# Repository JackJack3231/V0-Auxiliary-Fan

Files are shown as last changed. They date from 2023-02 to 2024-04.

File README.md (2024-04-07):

# V0 Auxiliary Cooling Fan

Auxiliary Cooling Fan Ducts for the Voron V0 3d-Printers, using either a 5015, 6028, 7530, 9733 or 12032 Blower fans.
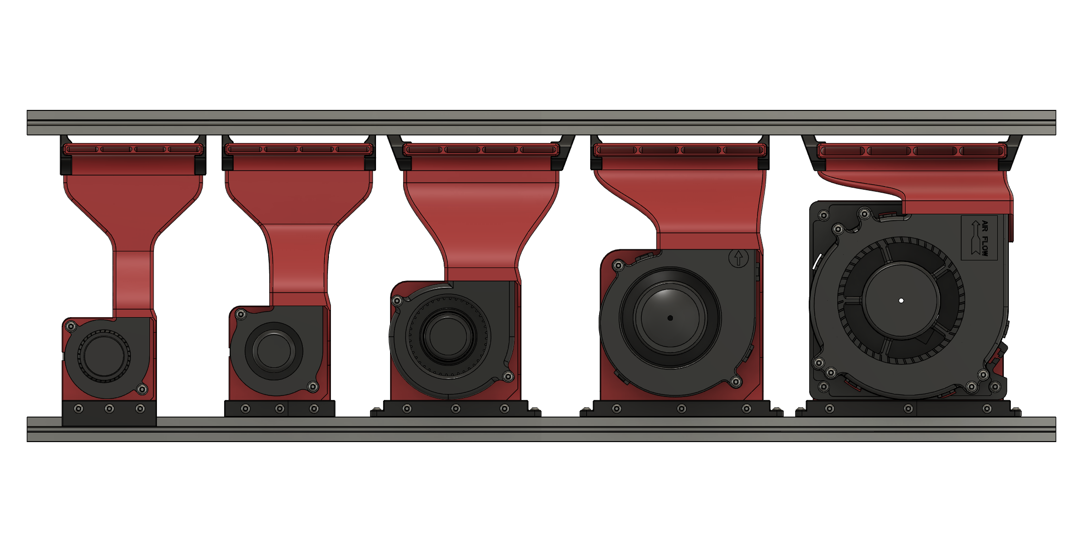
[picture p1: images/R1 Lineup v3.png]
Lineup of all Ducts


Below the 6028 Fan and duct installed in a v0.2 using the screw mounts.
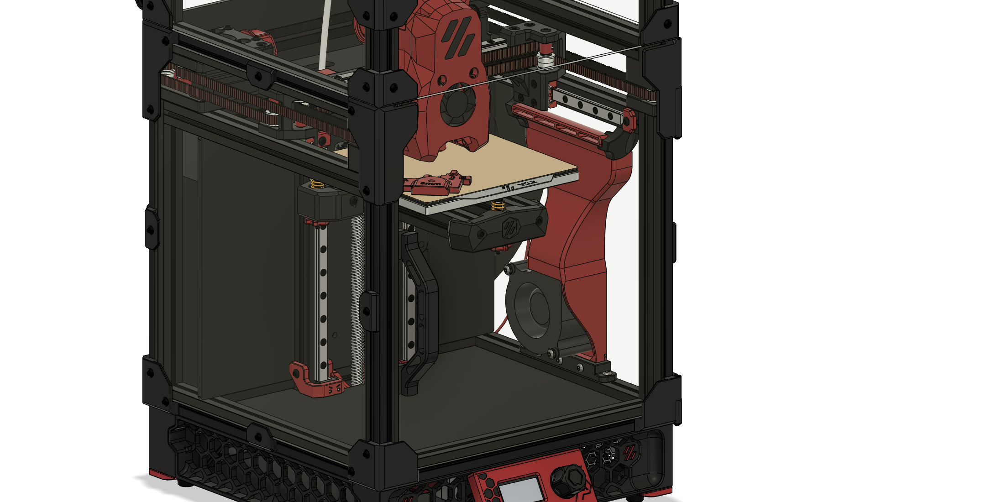
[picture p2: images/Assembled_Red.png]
5015 Fan installed


The ducts can be easily installed after the Printer has already been fully assembled, as there are mounting options that don't require preloaded nuts in the extrusion slots.

Since the [R1 release](#2023-08-15-R1-Release) there are now 3 mounting options:

1. (Legacy) Clamp-Mount: this one just clamps the duct to the bottom extrusion. This was an easy way to secure the ducts, however the ducts were prone to come loose from vibrations and could tilt into the print volume, colliding with the toolhead. This version is no longer recommended.
2. Screw-Mounts to secure the bottom and top of the ducts to the frame. These allow the most secure installation, however you will need preloaded M3 nuts in the slots of the extrusion (2 at the bottom and 2 at the top). Due to space constraints installing these Mounts (especially the top ones) can be rather difficult on the larger fan ducts with the frame assembled.
3. Twist-Mounts that get inserted into the extrusion slot and twisted 90° to secure to the frame. These provide a very solid mount while not needing preloaded M3 nuts and therefore are the recommended installation method for already fully assembled printers. If these are too tight or too loose after installation you can adjust the CAD-Files to improve the mount, a [guide is provided in the docs folder](docs/CAD_Twist_Tightness.md). There also is an alternative stronger version of the bottom twist mounts which don't rely on layer adhesion as much and should therefore be much stronger than the standard ones. The stronger mounts require 2 additional Heatsets and M3x12 screws.

All of these mounting options use the same main duct bodies, so you could also mix and match as you want. For Example if you used a Nevermore filter before you could use the 2 M3 nuts in the bottom extrusion to secure the bottom of the duct with a screw mount and the top with the twist mounts.

**No matter what mount you choose it is highly recommended you use one of the top mounts to ensure proper alignment towards the print bed and avoid the duct to collide with the toolhead.**

The ducts come in 2 Versions: A Unibody Version for which you'll need a larger Printer as it is 170 mm long and a 2 Piece Version which you can print on a V0 and glue together after printing.

I have not done any CFD-Simulation on these shrouds, so they definitely could be better.

Currently, there are ducts for the following Blower Fan sizes available:

- [50x15mm](/ducts/5015/)
- [60x28mm](/ducts/6028/)
- [75x30mm](/ducts/7530/)
- [97x33mm](/ducts/9733/)
- [120x32mm](/ducts/12032/)

There also are ducts that target their airflow 3 mm lower than the MiniSB for people using higher flow toolheads where the nozzle sits slightly lower in the [UHF Folder](ducts/_UHF/). **This is not required for High-Flow setups that don't change the nozzle height like chirpy's [Rapid Burner](https://github.com/chirpy2605/voron/tree/main/V0/Rapid_Burner)**.

I also started adding ducts, that I was requested to make for specific setups, to the repo. You will find these in the [Customs Folder](/ducts/_Customs/).

### Warning about Tolerances

There seems to be quite a bit of variance in the exact mounting hole patterns on these blower fans, especially the larger ones. So you could run into compatibility issues and need to adjust the model in CAD. I used GDSTIME fans for all my tests, so these should work.

Additionally, the width of the slots on the MakerBeamXL or LDO Extrusions can vary a lot. These generally are specced at 3-3.2 mm wide. The ducts were designed with a 3.2 mm thick part that slots into the extrusion. This was made to ensure a snug fit, however on some frames it could be very difficult/impossible to slot in. So either you can just print it and sand down the bottom part if needed or measure your frame before printing and adjust in CAD for the measured slot thickness.

### Overhang Test

For Comparison Pictures of the cooling Performance check the [Overhang Tests](/docs/OverhangTests.md) Document. These are currently outdated as they use the old ducts from before the R1 Release.

## Print Settings

As these parts don't hold any high loads you don't have to print these according to the Voron Guidelines. 3 Perimeters with 25% Infill are more than enough.

## Stuff to keep in mind

### Connecting the fan

You'll need a way to connect the fan, there are a few ways to do this outlined in the [Connecting the fan](/docs/connecting_fan.md) documentation.

### Shroud Clearance

If you have LEDs or a Camera mounted to the underside of the Y-axis extrusions these will likely collide with the fanshroud, so you might need to move the LEDs to the top.

## BOM

Depending on your choice of mount and fan the BOM changes. The parts for the mounts are the same, regardless of fan:
| Part | Quantity | Notes |
| --- | --- | --- |
| M3x5x4 Heatset Insert | 3 | for all mounts |
| M3x16 BHCS | 3 | for clamp mount |
| M3x12 BHCS | 2 | for screw and twist mount |
| M3x8 BHCS | 2 | for bottom screw mount |
| M3x6 BHCS | 2 | for top screw mount |
| Superglue | | only if using a 2 piece duct |
| VHB-Tape | | for top mounts |

**For the stronger twist mounts you will need 2 more Heatsets and M3x12 screws, so 5 Heatsets and 5 M3x12 screws in total.**

BHCS can be substituted for SHCS.

Additionally, you will need some Hardware to secure the fan. See the specific README of each version for a list of additionally required parts.

## Assembly instructions

Refer to the [General Assembly Instructions](/docs/general_assembly.md) documentation and the additional information in the README of each specific duct.

## Firmware Configuration

There are example klipper configs with macros and display entries provided. These allow easy control of the fan and even Slicers like BambuStudio or OrcaSlicer to control the fan with G-Code.

Refer to the [Firmware and Slicer Configuration](/docs/firmware_slicer.md) documentation.

## Credits

Thanks to the Voron Team for their great work on the V0 Printer: [Voron Design](https://vorondesign.com/voron0.2)

Following Fan Models were used in CAD:

- [Radial Cooling 5015 Fan (50 mm) DC12V](https://grabcad.com/library/radial-cooling-5015-fan-50mm-dc12v-1) by
  Aleksandr Ivanov
- [Basic 6028 Blower Model](https://www.thingiverse.com/thing:4270101) by kelvinA
- [Gamma 28 Blower Fan 76×30 mm](https://grabcad.com/library/gamma-28-blower-fan-76x30mm-1) by Pokai Chang
- [CBM-979433S-125-467](https://www.cuidevices.com/product/thermal-management/dc-fans/centrifugal-blowers/cbm-979433s-125-467) by CUI Devices
- [CBM-A232B-120-457](https://www.cuidevices.com/product/thermal-management/dc-fans/centrifugal-blowers/cbm-a232b-120-457) by CUI Devices

## Changelog

### 2024-04-07
- Add WIP Dual 5015 duct

### 2024-02-14
- Add 12032 Hex-Zero variant
- Add Stronger Bottom Twist Mount Variant. This does not rely on layer adhesion nearly as much as the standard version, so it should be a lot stronger. However, you will need 2 additional Heatsets and 2 M3x12 screws.
- Moved Mounts to separate sub-folders for better organization

### 2023-12-23

- Updated slot-bar to be a bit flexible and increase compatibility with different extrusion slot widths, while still providing some stiffness
- Added first custom duct model for the Hex-Zero with a 75x30 mm blower

### 2023-08-25

- Add experimental 5015 & 6028 ducts with clearance for klicky probes

### 2023-08-15 R1 Release

- Remade all ducts to make CAD cleaner, wall thicknesses more consistent and the design more consistent overall
- Adjusted ducts to reduce back pressure and improve overall cooling performance (12032 Version seems to still have a bit of a back pressure issue, but is far better than the old design).
- Increased thickness of bottom bar that slots into the extrusion for more rigid mount. Tolerances of these slots are quite big, so on some frames it could get tight.
- Added Cable-Channels to rear for tidier wire routing
- Added Screw-Mounts for the bottom and the top of the ducts (Require preloaded M3 nuts)
- Added "Twist"-Mounts for the bottom and the top of the ducts
- Improvements to Supports, resulting in better print results. However, these are slightly harder to remove.
- In addition to STEP Files I also exported the source Fusion 360 Files, allowing for easier Modification and understanding of how these ducts were created.
- Updated Documentation to reflect these changes
- Added links to the used CAD-Files for the fans

Changes made to ducts to improve cooling performance:

- 6028: Duct Outlet is now 85 mm wide (before 80 mm)
- 7530: Duct Outlet is 90 mm wide and 3.5 mm high (before 80 mm and 3 mm respectively)
- 9733: Duct Outlet is 100 mm wide and 4 mm high (before 80 mm and 3 mm respectively)
- 12032: Duct Outlet is 110 mm wide and 5 mm high (before 90 mm and 3 mm respectively)

All had slight changes to the internal flow guide geometry to (hopefully) improve cooling performance.

Known Issue: The 7530 duct still has higher airflow on the left side than on the right side, at least at 100% speed. Will need to rework the internal flow guides some time in the future.

### 2023-06-24

- Add centered Top Part for the 12032 Duct for better alignment when installed on the left side of the printer. Deprecated old version.

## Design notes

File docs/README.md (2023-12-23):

# Documentation

In this folder you will find some general documentation, that has been split into extra files to keep the README files to a reasonable Length.

## Current Documentation

### CAD Guide: [Adjusting Duct Height](CAD_Outlet_Height.md)

### CAD Guide: [Adjusting Twist Mount Tightness](CAD_Twist_Tightness.md)

### [Options to connect the fan](connecting_fan.md)

### [Firmware and Slicer configuration](firmware_slicer.md)

### [General Assembly Instructions](general_assembly.md)

### [Overhang Tests](OverhangTests.md)

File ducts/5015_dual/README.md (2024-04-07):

# WIP: Dual 5015 Blower Fan Duct

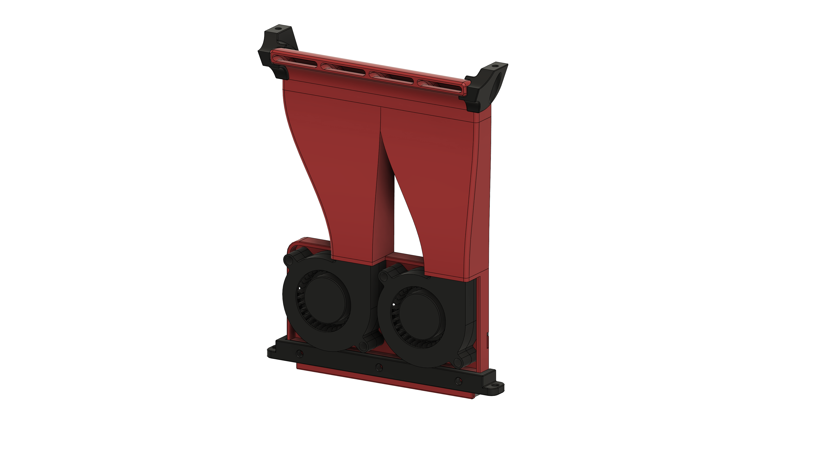
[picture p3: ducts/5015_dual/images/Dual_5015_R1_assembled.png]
Dual 5015 Duct


## WIP
**Currently this variant is untested!**

 - There is no 2 Piece variant available, so you need a large enough printer to print these parts
 - For the bottom twist mount there is only the "strong" variant available

## BOM
These parts are required in addition to the [General BOM](/README.md#bom)
| Part | Quantity | Notes |
| --- | --- | --- |
| M3x5x4 Heatset Insert | 4 | |
| 5015 Blower Fan | 2 | 5V or 24V depending on your setup |
| M3x20 BHCS | 4 | M3x18 also works, then you don't need the printed spacer |
| M3 Washer | 4 | optional, only to make better contact with the fan |

## Printed Parts

Print the parts according to your choice of mount. If you are using M3x20 BHCS don't forget to print 2 of the spacers.

## Assembly Instructions
Follow the [General Assembly Instructions](/docs/general_assembly.md).

To secure the fans to the duct use the M3x20 BHCS with a washer and the printed spacer. Alternatively use M3x18 BHCS with a washer but without the spacer.

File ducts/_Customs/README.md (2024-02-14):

# Custom fan ducts

In this folder you will find ducts that I made upon request for specific setups.
Feel free to reach out to me if you need a custom duct made for your printer and fan setup, however I cannot guarantee that I will have the time to actually make it.

Also, I will only update these upon request.

BOM is generally the same as the standard versions unless specifically called out.

| Printer/Setup | Notes | Link to Printer |
| --- | --- | --- |
| [75x30 mm for Hex-Zero](Hex-Zero/7530/) | Designed only for the right side, as left has the Probe Dock | [Hex-Zero GitHub](https://github.com/Alexander-T-Moss/Hex-Zero) |
| [120x32 mm for Hex-Zero](Hex-Zero/12032/) | Designed only for the right side, as left has the Probe Dock | [Hex-Zero GitHub](https://github.com/Alexander-T-Moss/Hex-Zero) |

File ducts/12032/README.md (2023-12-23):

# 12032 Blower Fan Duct

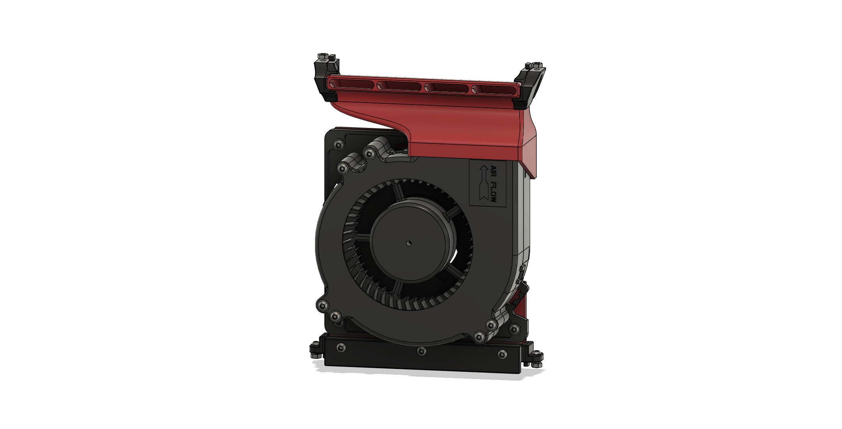
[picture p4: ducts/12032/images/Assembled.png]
12032 Duct Assembled


## BOM

| Part | Quantity | Notes |
| --- | --- | --- |
| M3x5x4 Heatset Insert | 9 | |
| 12032 Blower Fan | 1 | 5V or 24V depending on your setup |
| M3x8 BHCS | 3 | |
| M3x35 BHCS | 6 | |
| M3 Washer | 9 | optional, only to make better contact with the fan |

These numbers of screws and Heatsets are to populate all the mounting holes of the fan.

The Fan I used was this [GDSTIME 12032 24V Dual Ball Bearing Blower Fan](https://www.aliexpress.com/item/1005005288258849.html)

## Printed Parts

Print the parts according to your choice of mount.

## Assembly Instructions

Follow the [General Assembly Instructions](/docs/general_assembly.md).

To secure the fan to the duct use the M3x8 BHCS with a washer to secure the corners of the fan and the M3x35 BHCS with a washer to secure the remaining 6 inner holes.

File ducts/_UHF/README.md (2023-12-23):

# UHF Ducts
Here you will find ducts with a 3 mm lower outlet to better target the air for longer toolheads/Hotends.

**These are not required for High Flow setups that don't change the nozzle height, like chirpy's [Rapid Burner](https://github.com/chirpy2605/voron/tree/main/V0/Rapid_Burner). If your setup has the nozzle at the same height as the stock Mini-Stealthburner you will need the "standard" ducts instead.**

If you need a different height for the outlet there is a [guide to edit the base Fusion360 CAD Files](/docs/CAD_Outlet_Height.md) in the docs' folder.

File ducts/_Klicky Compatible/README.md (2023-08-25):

# Klicky compatible fan ducts
These ducts are designed to leave space at the front right corner for the klicky mounts are lower to make space for the carrier part on the cowling and blow the air across the bed at an angle.

**These are completely untested and highly experimental!**

So far there are unibody ducts for the 5015 and 6028 fans. The bottom mounts are the same as for the standard ducts. Due to the angle of the ducts there are new top mounts.

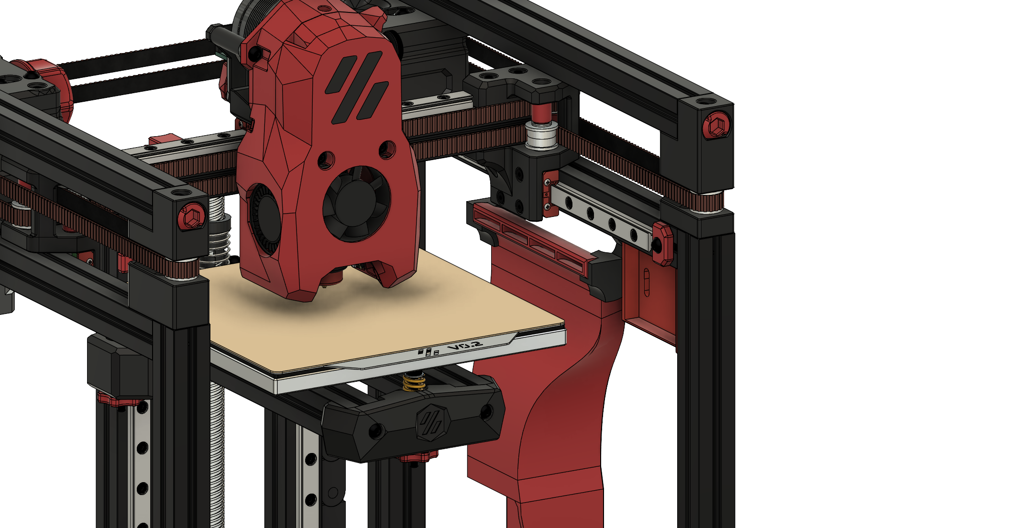
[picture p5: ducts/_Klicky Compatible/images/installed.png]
Installed Duct


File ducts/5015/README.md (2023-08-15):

# 5015 Blower Fan Duct

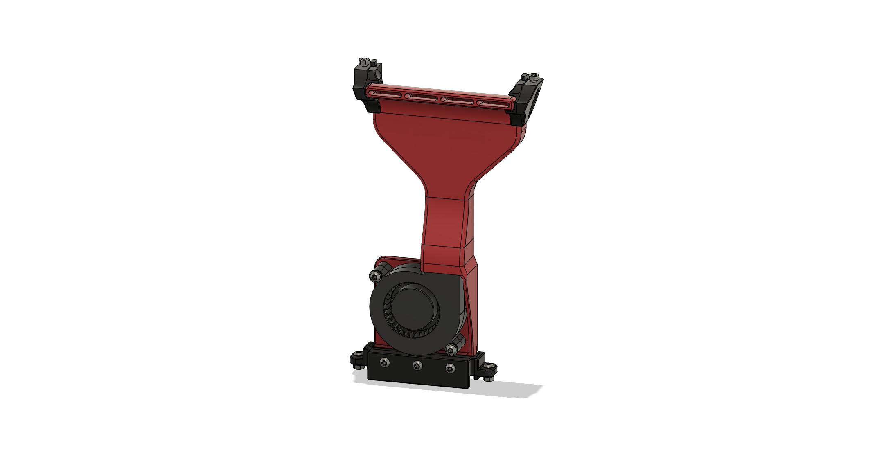
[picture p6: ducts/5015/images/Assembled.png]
5015 Duct Assembled


## BOM
These parts are required in addition to the [General BOM](/README.md#bom)
| Part | Quantity | Notes |
| --- | --- | --- |
| M3x5x4 Heatset Insert | 2 | |
| 5015 Blower Fan | 1 | 5V or 24V depending on your setup |
| M3x20 BHCS | 2 | M3x18 also works, then you don't need the printed spacer |
| M3 Washer | 2 | optional, only to make better contact with the fan |

The Fan I used was this [GDSTIME 5015 24V Dual Ball Bearing Blower Fan](https://www.aliexpress.com/item/32865977791.html)

## Printed Parts

Print the parts according to your choice of mount. If you are using M3x20 BHCS don't forget to print 2 of the spacers.

## Assembly Instructions
Follow the [General Assembly Instructions](/docs/general_assembly.md).

To secure the fan to the duct use the M3x20 BHCS with a washer and the printed spacer. Alternatively use M3x18 BHCS with a washer but without the spacer.

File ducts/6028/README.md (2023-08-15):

# 6028 Blower Fan Duct

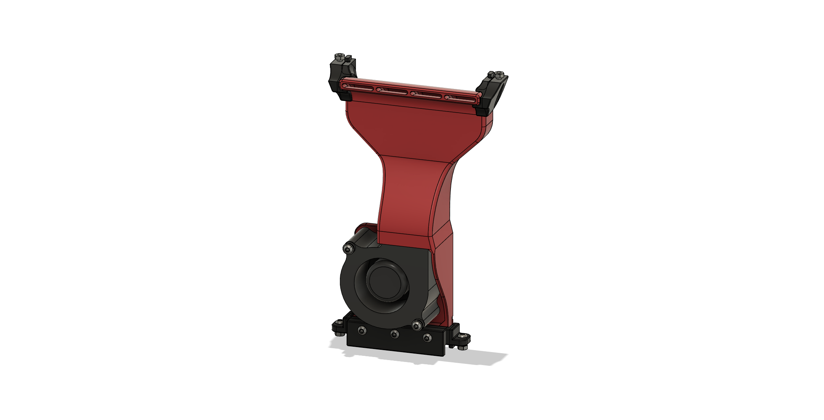
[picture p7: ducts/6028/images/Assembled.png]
6028 Duct Assembled


## BOM
These parts are required in addition to the [General BOM](/README.md#bom)
| Part | Quantity | Notes |
| --- | --- | --- |
| M3x5x4 Heatset Insert | 2 | |
| 6028 Blower Fan | 1 | 5V or 24V depending on your setup |
| M3x35 BHCS | 2 | |
| M3 Washer | 2 | optional, only to make better contact with the fan |

The Fan I used was this [GDSTIME 6028 24V Dual Ball Bearing Blower Fan](https://www.aliexpress.com/item/1005003792895461.html)

## Printed Parts

Print the parts according to your choice of mount. Print 2 of the spacers for use with the M3x35 BHCS.

## Assembly Instructions
Follow the [General Assembly Instructions](/docs/general_assembly.md).

To secure the fan to the duct use the M3x35 BHCS with a washer and the printed spacer.

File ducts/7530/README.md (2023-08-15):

# 7530 Blower Fan Duct

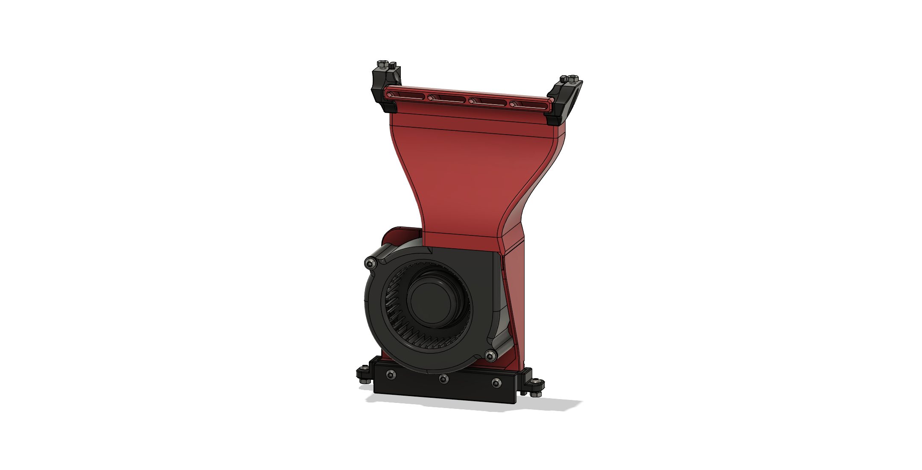
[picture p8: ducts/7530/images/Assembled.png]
7530 Duct Assembled


## BOM
These parts are required in addition to the [General BOM](/README.md#bom)
| Part | Quantity | Notes |
| --- | --- | --- |
| M3x5x4 Heatset Insert | 2 | |
| 7530 Blower Fan | 1 | 5V or 24V depending on your setup |
| M3x35 BHCS | 2 | |
| M3 Washer | 2 | optional, only to make better contact with the fan |

The Fan I used was this [GDSTIME 7530 24V Dual Ball Bearing Blower Fan](https://www.aliexpress.com/item/1005002663971820.html)

## Printed Parts

Print the parts according to your choice of mount. Print 2 of the spacers for use with the M3x35 BHCS.

## Assembly Instructions
Follow the [General Assembly Instructions](/docs/general_assembly.md).

To secure the fan to the duct use the M3x35 BHCS with a washer and the printed spacer.

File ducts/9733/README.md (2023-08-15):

# 9733 Blower Fan Duct

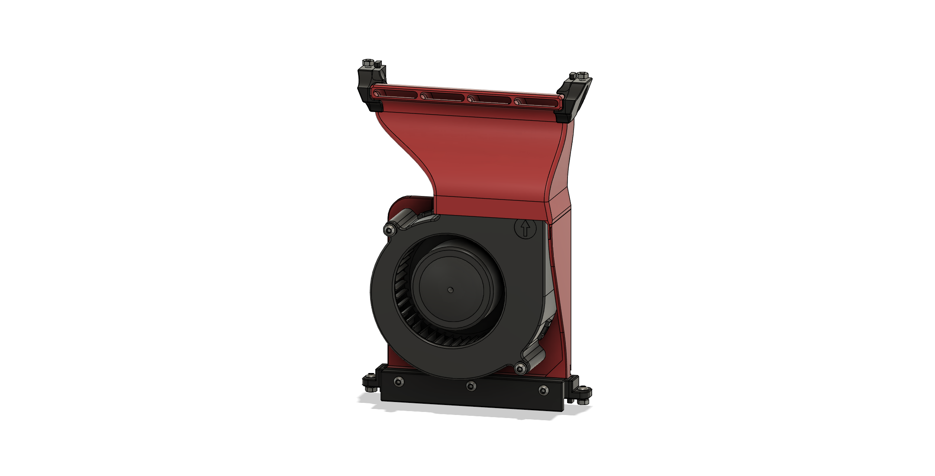
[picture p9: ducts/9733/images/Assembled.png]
9733 Duct Assembled


## BOM

These parts are required in addition to the [General BOM](/README.md#bom)
| Part | Quantity | Notes |
| --- | --- | --- |
| M3x5x4 Heatset Insert | 2 | |
| 9733 Blower Fan | 1 | 5V or 24V depending on your setup |
| M3x40 BHCS | 2 | |
| M3 Washer | 2 | optional, only to make better contact with the fan |

The Fan I used was this [GDSTIME 9733 24V Dual Ball Bearing Blower Fan](https://www.aliexpress.com/item/32622626365.html)

## Printed Parts

Print the parts according to your choice of mount. Print 2 of the spacers for use with the M3x40 BHCS.

## Assembly Instructions

Follow the [General Assembly Instructions](/docs/general_assembly.md).

To secure the fan to the duct use the M3x40 BHCS with a washer and the printed spacer.

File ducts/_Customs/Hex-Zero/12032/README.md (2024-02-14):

# 12032 for Hex-Zero

Custom designed duct and mount to fit the ginormous 12032 Blower fans into a Hex-Zero.

**This is currently untested.** Especially the clearance for the z-axis drag chain could be problematic, a "fixed" chain end on the rail mount is recommended to prevent the drag chain from rubbing against the fan body.
The wall thickness was also reduced to 1 mm from 2 mm to make space for the ducting, however this also means that the duct part is weaker.

All the printed parts were made specifically for the Hex-Zero and none of the original duct are reused.

Also, the way the bottom mount and duct attach to the fan has changed, you will need to install 3 Heatsets into the 3 outer mounting holes of the Blower Fan (see [Heatset Locations](#heatset-locations)).

## BOM

| Part | Quantity | Notes |
| --- | --- | --- |
| M3x5x4 Heatset Insert | 3 | |
| 12032 Blower Fan | 1 | 5V or 24V depending on your setup |
| M3x12 BHCS | 2 | |
| M3x6 BHCS | 1 | |

If you use the screw mounts you will need a M3x6 BHCS and M3 Nut for each mounting point (4 in total, 2 for the bottom and 2 for the top mounts).

## Printed Parts
You will need to print:
- 1x 12032_R1_Hex-Zero_Right_Top
- 2x Top Mount of your choice (Screw or Twist)
- 2x Bottom Mount of your choice (Screw or Twist)

## Images
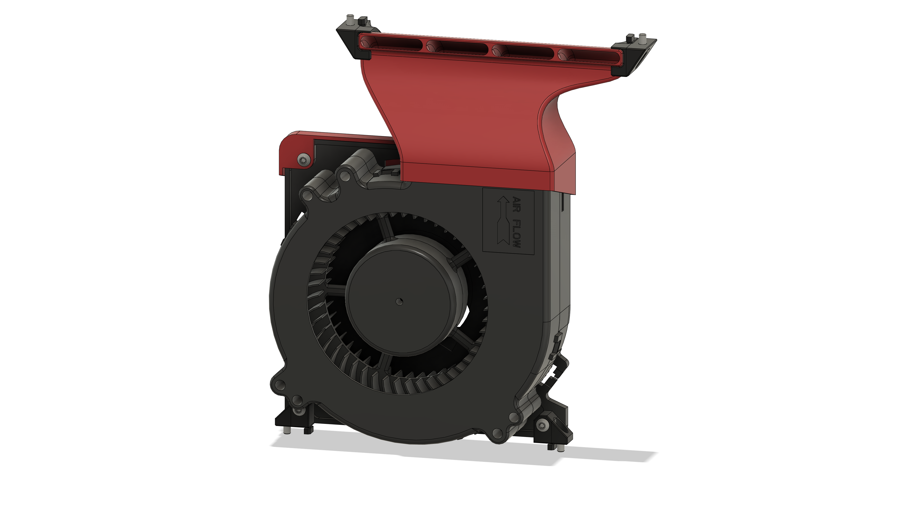
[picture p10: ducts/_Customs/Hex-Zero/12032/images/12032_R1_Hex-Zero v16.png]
12032 Hex-Zero

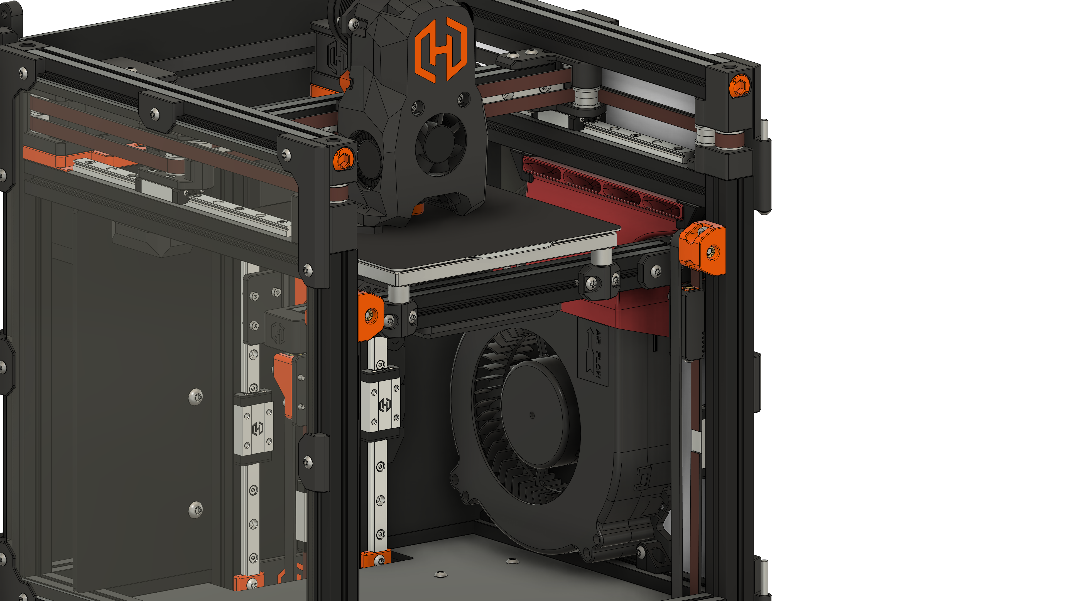
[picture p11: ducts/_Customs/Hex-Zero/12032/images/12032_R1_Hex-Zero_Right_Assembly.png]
12032 Hex-Zero Installed

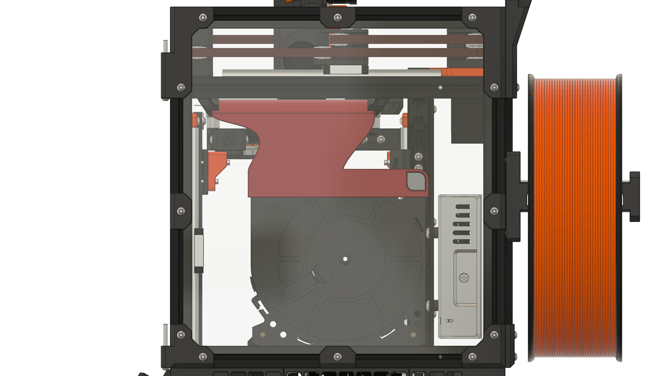
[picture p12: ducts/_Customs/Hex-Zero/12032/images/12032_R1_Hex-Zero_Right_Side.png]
12032 Hex-Zero Bed clearance


### Heatset Locations
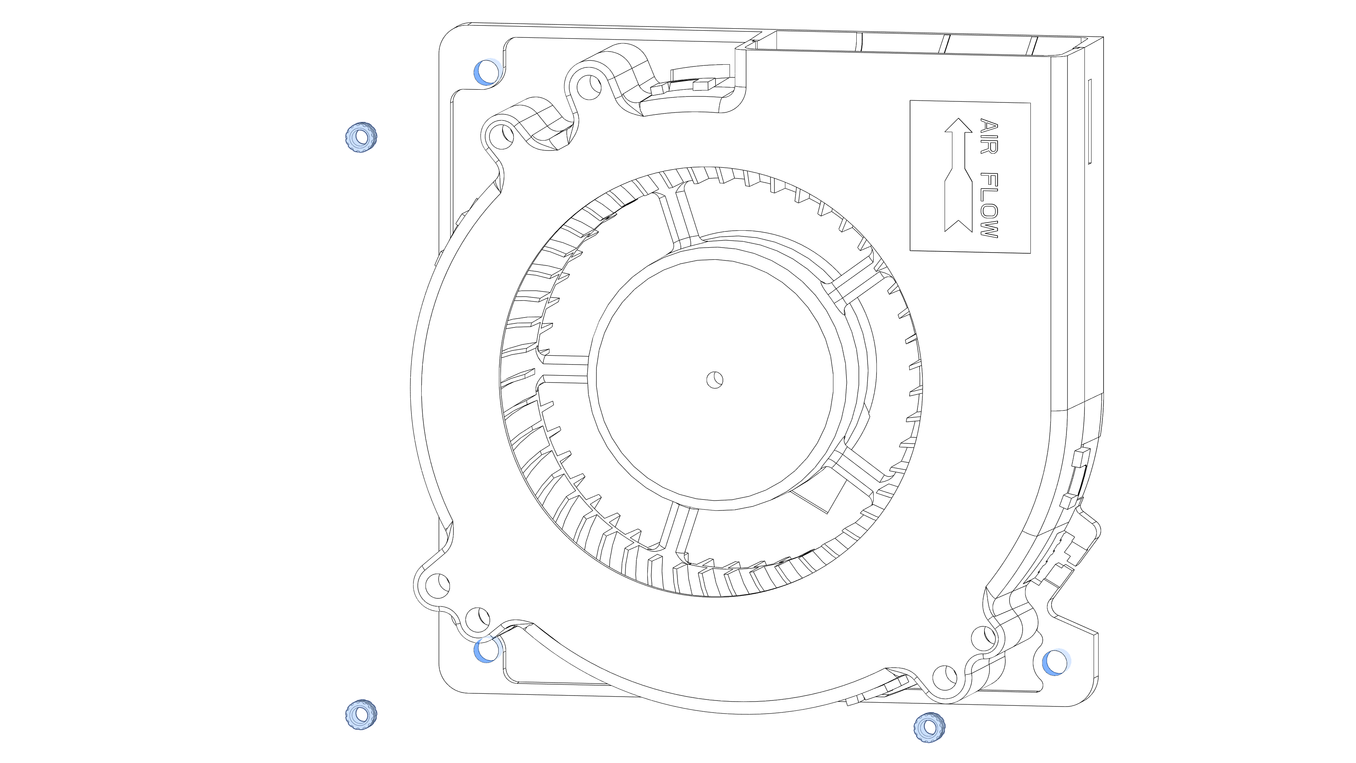
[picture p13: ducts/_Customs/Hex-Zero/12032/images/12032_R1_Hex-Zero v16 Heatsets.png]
12032 Hex-Zero Heatsets


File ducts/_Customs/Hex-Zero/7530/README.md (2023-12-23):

# 7530 for Hex-Zero

Custom designed duct to have the outlet at the proper height and clear the Bed Assembly.
The duct is confirmed to fit and work.

The bottom mount parts are the same as the standard duct, so get your choice from the [7530 folder](/ducts/7530/).

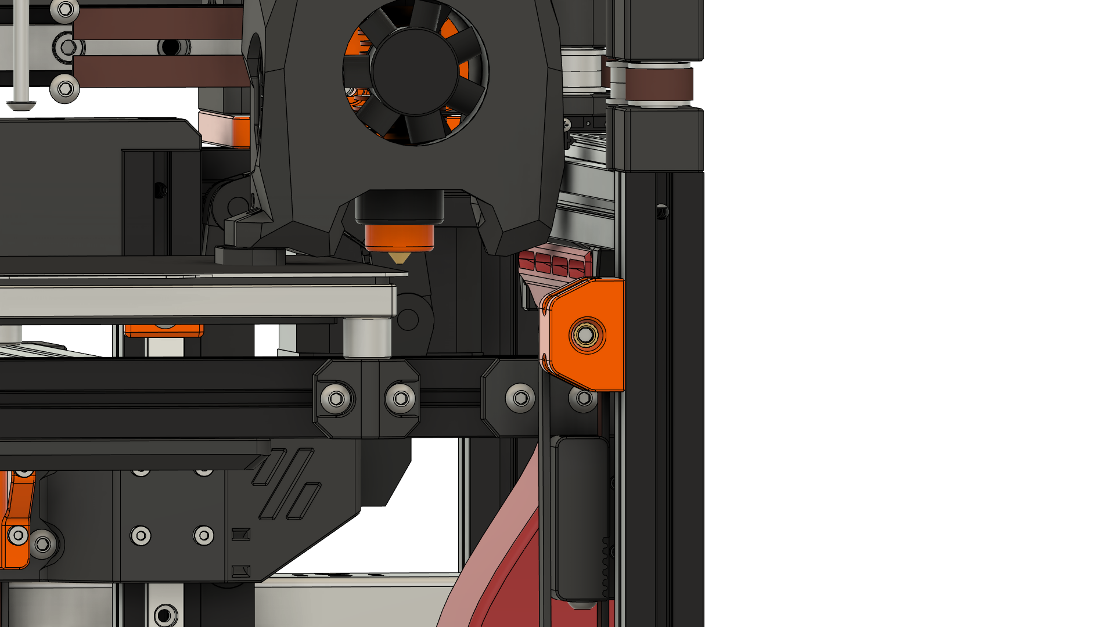
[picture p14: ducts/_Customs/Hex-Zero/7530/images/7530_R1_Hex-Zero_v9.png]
7530 Hex-Zero Height

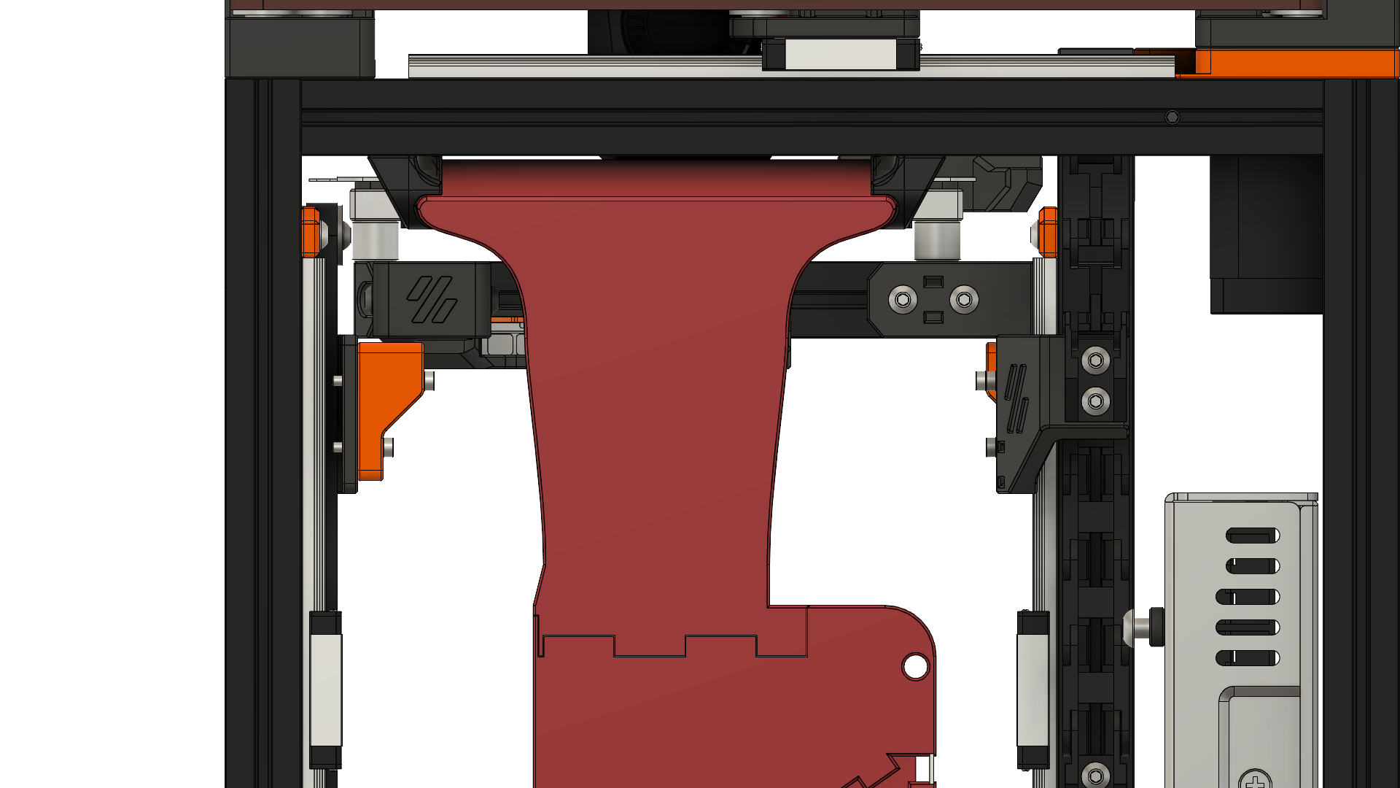
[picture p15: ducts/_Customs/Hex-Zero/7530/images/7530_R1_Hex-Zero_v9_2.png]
7530 Hex-Zero Bed clearance


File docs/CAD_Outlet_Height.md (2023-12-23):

# Adjusting the Height of the ducts
If you need a different height for the ducts, because you have a different length toolhead installed, or you just want to play around with the geometry of the outlets you can import the f3z CAD file to Fusion360 and by just editing one sketch achieve your goal.

## 1. Import the f3z CAD-File
Select `File > Open...` select the duct you wish to edit and upload it to Fusion360. This will take a little of time. Then Open the Project File.
## 2. Select the first Sketch in the timeline and edit it
To adjust the height of the Outlet change the highlighted 3 mm dimension. 3 mm is the value to target the nozzle height of the Mini StealthBurner. So if your nozzle is for example 2.5 mm lower you'll have to add this to the 3 mm: 3 mm+2.5 mm=5.5 mm is the new Dimension you want to enter here. Afterwards click finish Sketch and wait for Fusion to do all the calculations.
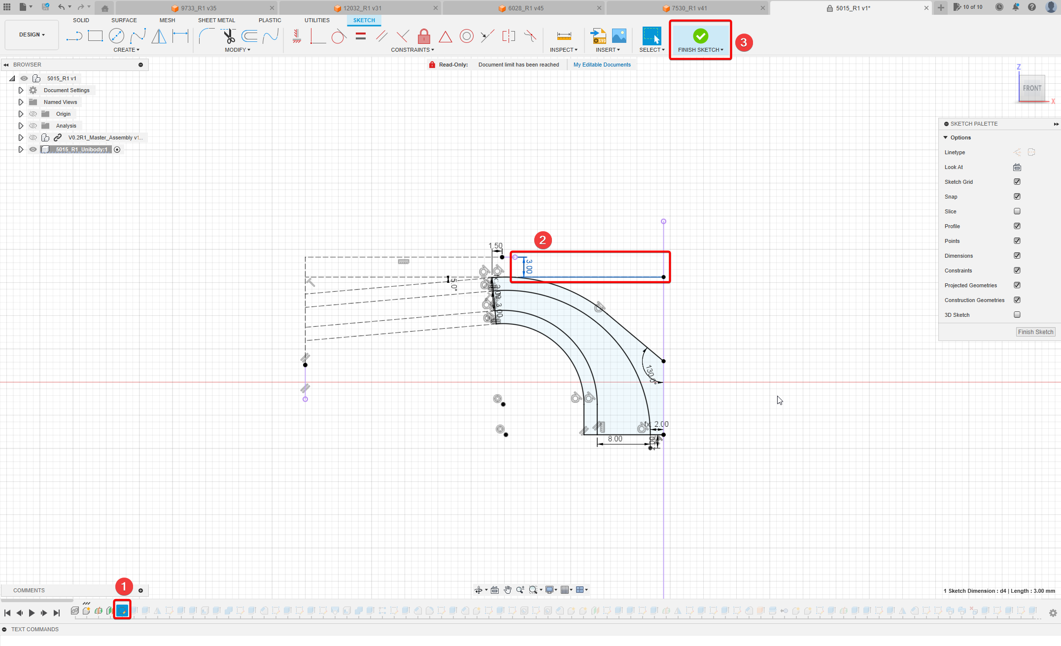
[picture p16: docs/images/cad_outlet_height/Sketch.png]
Sketch


## 3. Afterwards you might get some Warnings or Errors pop up at the bottom right
Generally the Yellow Warnings can just be ignored. These often come from some edges on chamfers/fillets getting combined and not needing a chamfer anymore.

If you get a red Error you will have to check in the timeline what operation is causing the Error. These usually also come from chamfers or fillets, these can most of the time be fixed by deselecting the edges in question.

## 4. Export the Bodies/Components
Now Export the parts that you need as STL's.

**Important** For the ducts export the components that contain the support structures as **one file** as otherwise the supports will be missing after the export.

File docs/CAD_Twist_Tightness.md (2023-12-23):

# Adjusting Twist Mount Tightness in CAD
There are 2 basic ways to adjust the tightness of the twist mount:
## 1: Adjusting the Parameter in Fusion360
How much the twist mounts press on the extrusion is controlled with a Parameter in Fusion360. So if you import the f3z CAD file you only need to got to `Modify > Change Parameters` and search for `Twist` and edit the value. Decreasing it makes the grip looser, increasing it makes it tighter.
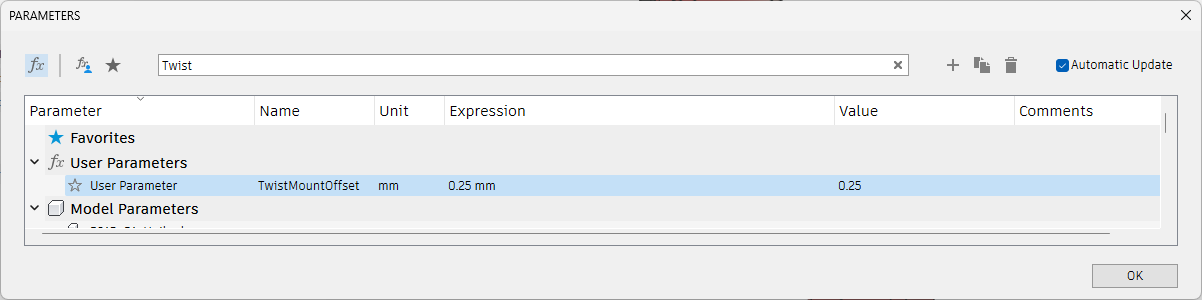
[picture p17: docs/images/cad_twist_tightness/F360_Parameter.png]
F360 Parameter

## 2: Manually moving the faces of the contact of the Twist mounts
This should work in basically all CAD software. Import the STEP File then isolate the Twist Mount Component.
Select the faces of the T-Bar that contact the extrusion and move the faces to adjust the tightness of the mount. Repeat this for all 4 of the twist mounts.
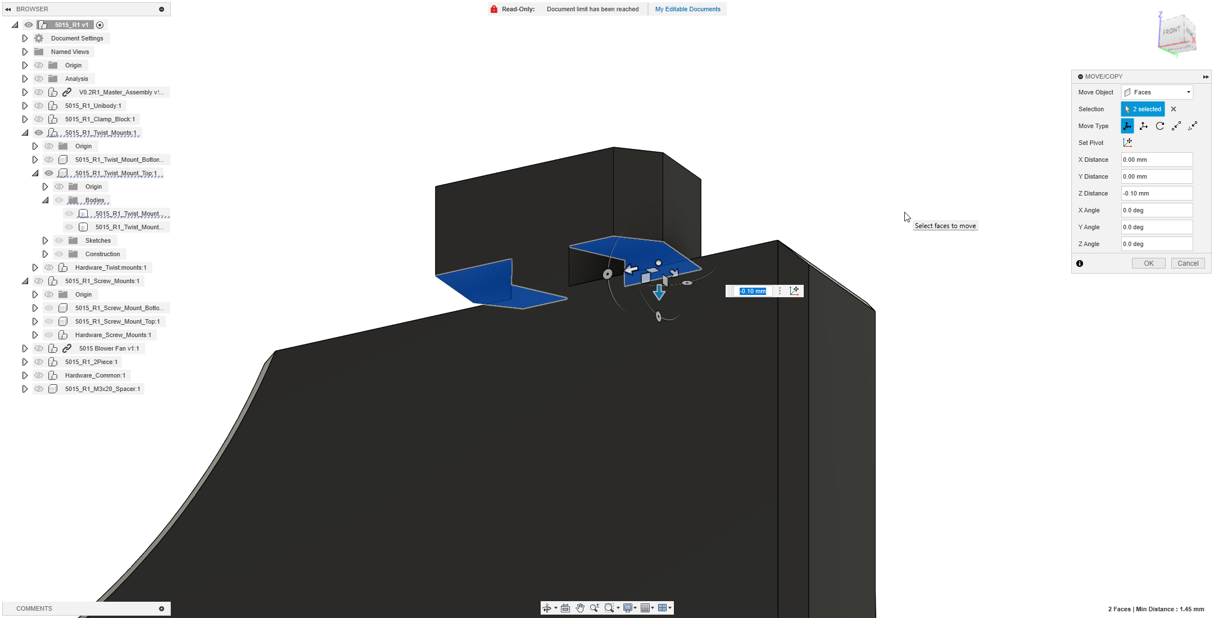
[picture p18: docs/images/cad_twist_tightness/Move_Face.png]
Move Faces


## After adjusting export the mount files as STL and print

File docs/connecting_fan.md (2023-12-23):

# Options to connect the fan

You will need a way to connect the fan to your printer. Here are some ways this could be achieved:

## MCU with enough fan ports

The easiest way would be to use a Fan-Port on your MCU, however most MCUs are already completely occupied by the Hotend-, Partcooling- and Controller-Fan. So you would need an MCU with more Fan-Ports, like the [Mellow Fly E3 Pro v3](https://www.aliexpress.com/item/1005002372751834.html) which has 4 Fan-Ports while having the same footprint as an Ender 3 Board (like BTT SKR E3).

## Additional MCU

Because Klipper supports multiple MCUs you could add another MCU however this one would need to be very small to fit the electronics compartment of the V0. One option would be [Timmit's Klipper Expander](https://github.com/VoronDesign/Voron-Hardware/tree/master/Klipper_Expander) over on the Voron-Hardware GitHub.

## CAN-Bus Toolhead Board

By using a CAN-Bus Toolhead board you are freeing up 2 Fan-Ports on your main MCU, because your hotend and partcooling fan are now connected to the CAN-Board. This would allow you to connect your auxiliary fan to the MCU.

## Raspberry Pi GPIO-Pin with Transistor/MOSFET

Alternatively you can run the fan of a GPIO-Pin of your Pi by using a Transistor or MOSFET. There are quite a few guides online on how to do this, like [this one from SENSORSIOT](https://www.sensorsiot.org/variable-speed-cooling-fan-for-raspberry-pi-using-pwm-video138/). You can ignore the Python-Script, as we will control the fan through Klipper (see [Klipper Configuration](firmware_slicer.md#klipper-configuration)). The IRLZ44N MOSFET has worked fine for me for both 5V and 24V Fans.

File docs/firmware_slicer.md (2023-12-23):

# Firmware and Slicer Configuration
## Klipper Configuration

All the values for the settings are what works for me with a GDSTIME 24V Dual Ball Bearing Fan. You might need to adjust these for your setup.

Copy the included `aux_fan.cfg` from the [firmware folder](/firmware/) to your klipper config folder and add `[include aux_fan.cfg]` to your `printer.cfg`.

Edit the `aux_fan.cfg` and replace the `PIN` in the `[fan_generic Aux_Fan]` section with the pin you have your fan connected to.

Klipper does not support controlling additional fans with `M106` and `M107` by default, so I added some replacement Macros which include a selection parameter `P` kinda like [Marlin](https://marlinfw.org/docs/gcode/M106.html) does. Index 2 gets matched to the Auxiliary cooling fan, because that is how BambuStudio and its forks (e.g. OrcaSlicer) control the auxiliary cooling fan.

Be sure to add a `M107` or `M106 P2 S0` to either your `PRINT_END`-macro or in the end-gcode of your slicer to make sure that the auxiliary fan and partcooling fan stops. Often there is only a `M106 S0` executed at the end, which only turns off the partcooling fan but not the Auxiliary fan.

The `aux_fan.cfg` also adds Controls for the auxiliary fan to the Display in the `Control` Menu, so you can also control the fan with an V0-Display.
These new controls should appear right beneath the partcooling fan inputs, if they don't, you might need to adjust the `index` value in `aux_fan.cfg`.
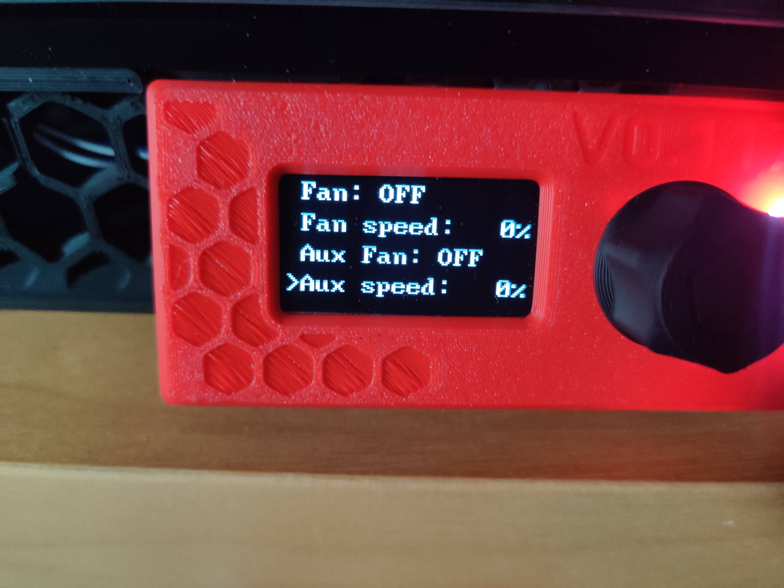
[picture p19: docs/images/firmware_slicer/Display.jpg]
DisplayEntries


### Config-Example: Fan connected to the Fan 3 Port (PB7) on a Mellow Fly E3 Pro v3:

```
...
[fan_generic Aux_Fan]
pin: PB7
...
```

### Config-Example: Fan controlled with MOSFET connected to GPIO13 on your Raspberry Pi and your Pi is configured in klipper with a `[mcu host]` section:

```
...
[fan_generic Aux_Fan]
pin: host:gpiochip0/gpio13
...
```

## Controlling the Fan

### Manual

After you have added the configuration to your klipper instance and reloaded klipper you should be able to control the fan using `SET_FAN_SPEED FAN=Aux_Fan SPEED=XX` where `XX` is a (decimal-) number between 0 and 1 (1 being 100%, 0.5 = 50% and so on).

If you are using Mainsail or Fluidd you should see a `Aux Fan` Slider right under the normal Partcooling-fan control, with which you can also set the fan speed.

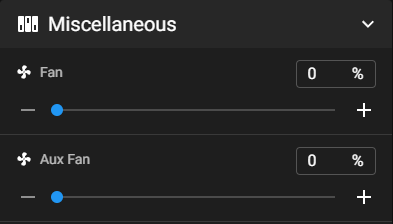
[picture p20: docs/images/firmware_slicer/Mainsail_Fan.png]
Mainsail Fan Control


### Slicer

There is no widespread support for auxiliary cooling fans in slicers.
The only one I know of is [BambuStudio](https://github.com/bambulab/BambuStudio) and its Forks (e.g. [OrcaSlicer](https://github.com/SoftFever/OrcaSlicer)). The way BambuStudio controls the auxiliary cooling fan is by sending a `M106 P2 Sxxx`, where `xxx` is the speed on a scale of 0 to 255. That is why there is an included Macro for Klipper that allows this G-Code to function with klipper.

#### BambuStudio

In the `Filament settings` window in the `Cooling section` set the auxiliary Cooling fan speed to what you want. This will enable the fan to the set speed after the first layers where the partcooling fan is disabled.
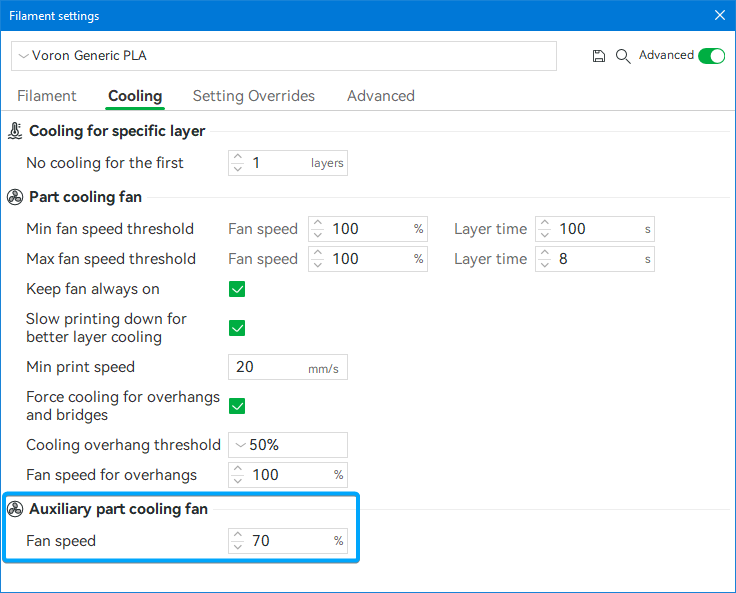
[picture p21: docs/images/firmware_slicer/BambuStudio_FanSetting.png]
BambuStudio Settings


#### OrcaSlicer

In the `Printer settings` under `Basic inormation` enable the `Auxilliary part cooling fan` setting. Then in the `Filament settings` set the fan speed to your wanted speed (like with standard BambuStudio).
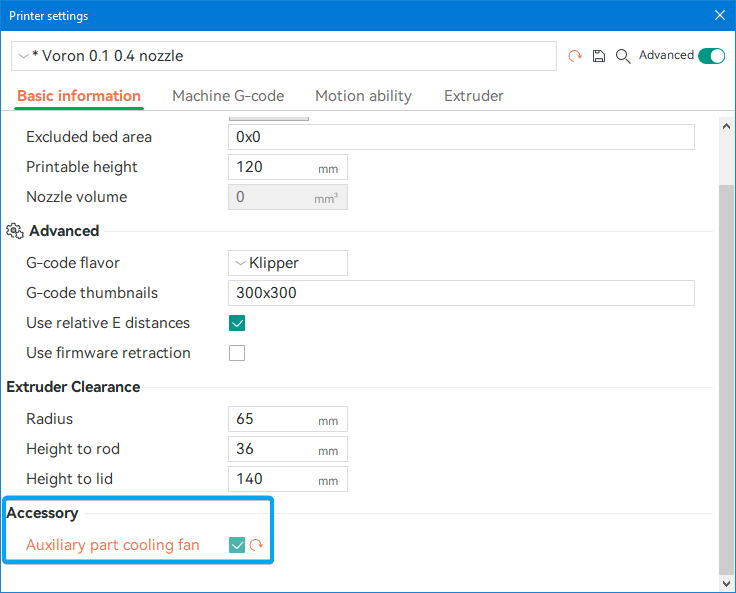
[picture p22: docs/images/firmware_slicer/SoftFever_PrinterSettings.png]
SoftFever PrinterSettings

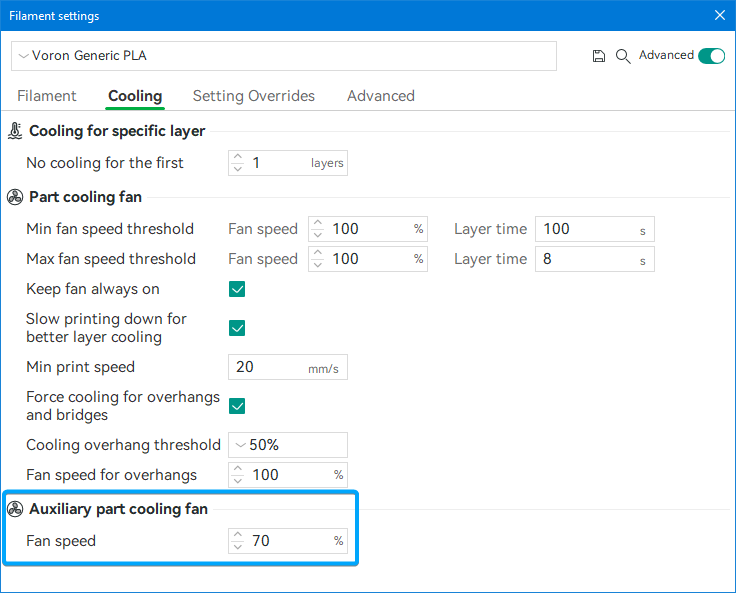
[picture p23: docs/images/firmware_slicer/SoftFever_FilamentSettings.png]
SoftFever FilamentSettings


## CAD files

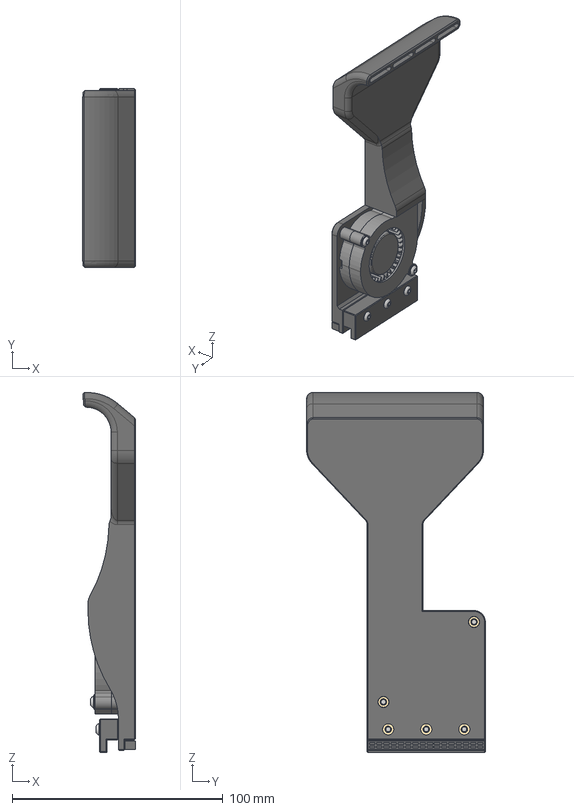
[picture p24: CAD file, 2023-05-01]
ducts/5015/CAD/Aux Fan v31.step
24.9 x 84.9 x 171.0 mm
turbine
top
bottom
M3x16BHCS_NO THREADS x 3
M3x18BHCS_NO THREADS x 2
DIN125 Washer x 2
M3 Threaded Insert x 5

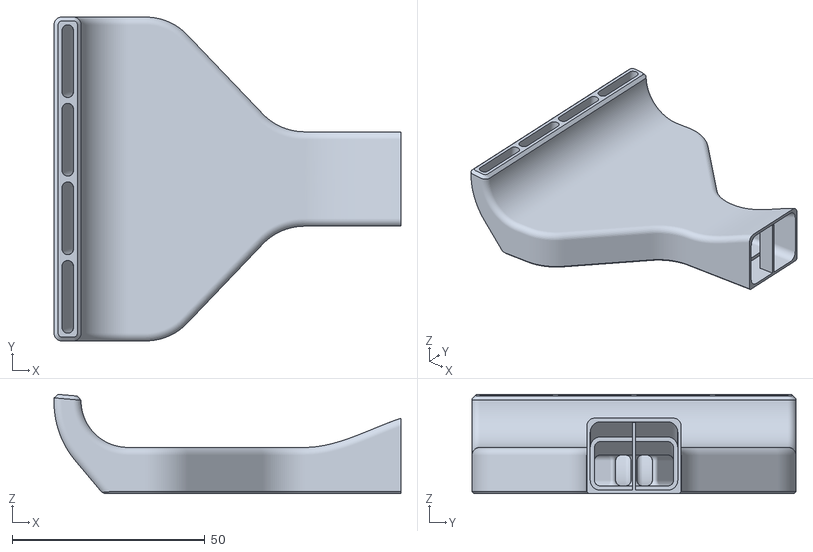
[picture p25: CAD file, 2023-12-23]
ducts/5015/STL/5015_R1_2Piece_Top.stl
90.0 x 84.0 x 25.7

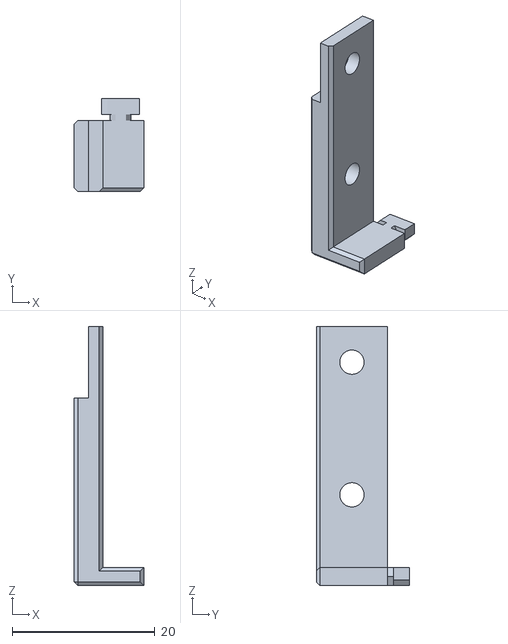
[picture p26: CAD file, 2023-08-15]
ducts/5015/STL/Twist_Mount/5015_R1_Twist_Mount_Right.stl
9.75 x 13.1 x 36.3

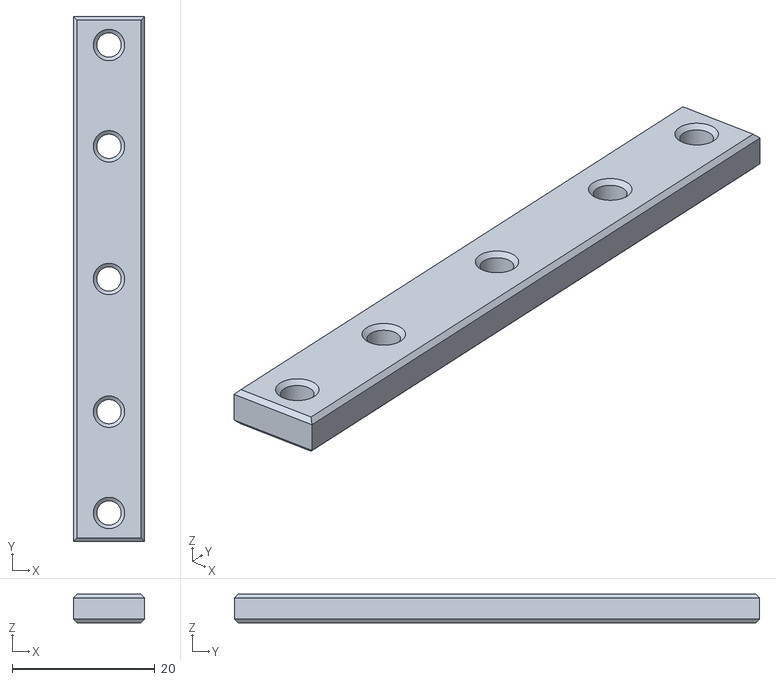
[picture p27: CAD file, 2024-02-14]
ducts/5015/STL/Twist_Mount_Stronger/5015_R1_Twist_Mount_Bottom_Stronger_Bar.stl
10.0 x 73.6 x 4.00

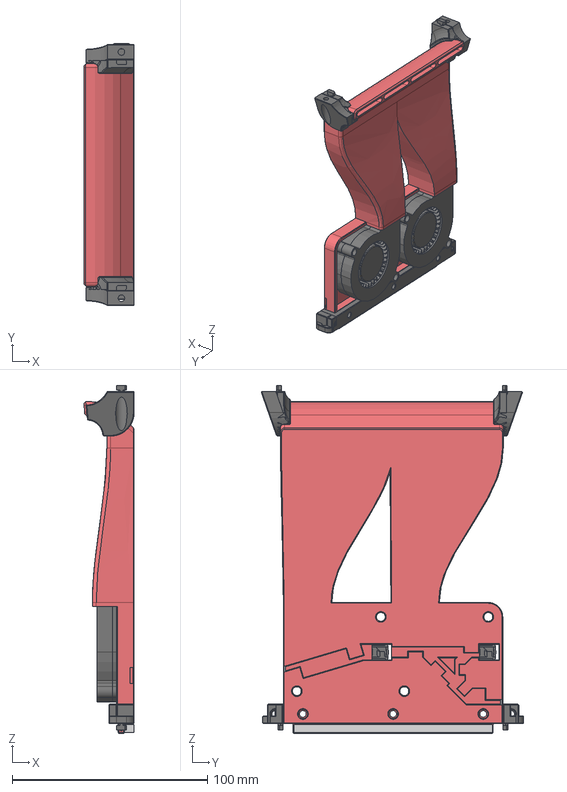
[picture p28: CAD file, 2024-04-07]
ducts/5015_dual/CAD/Dual_5015_R1 v8.step
25.7 x 134.3 x 178.1 mm
5015 Blower Fan x 2
BrimBlocker
Supports
Dual_5015_ScrewMount_Bottom
Dual_5015_ScrewMount_Top_Right
Dual_5015_ScrewMount_Top_Left
Dual_5015_TwistMount_Bottom_Bar
Dual_5015_TwistMount_Bottom_Left
Dual_5015_TwistMount_Top_Right
Dual_5015_TwistMount_Bottom_Right
Dual_5015_TwistMount_Top_Left

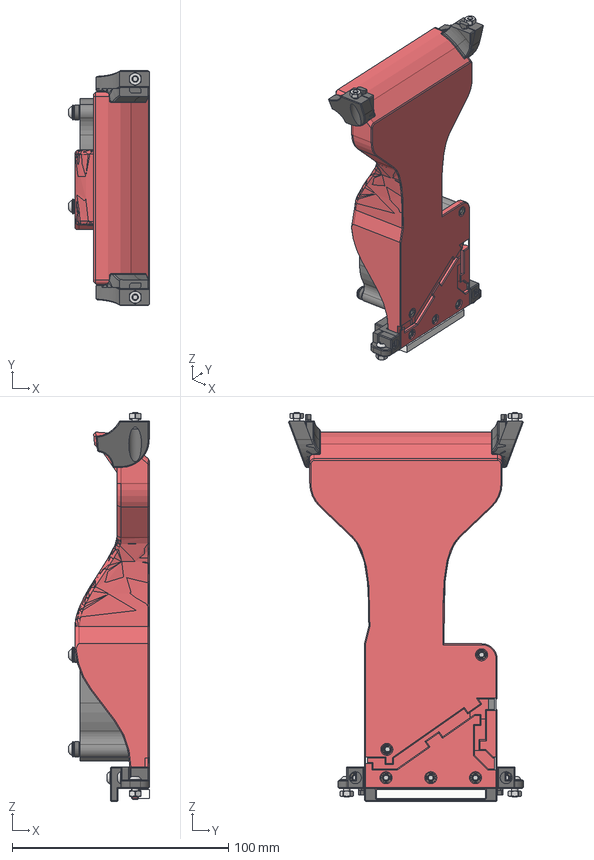
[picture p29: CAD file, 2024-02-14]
ducts/6028/CAD/6028_R1 v47.step
37.3 x 108.7 x 180.0 mm
DuctSupports x 2
BrimBlocker x 2
6028 Blower Fan
M3x16 BHCS x 3
6028_R1_Twist_Mount_Bottom
6028_R1_Twist_Mount_Bottom_Stronger
6028_R1_Twist_Mount_Top
M3x12 BHCS x 8
M3 Threaded Insert x 7
6028_R1_Screw_Mount_Bottom
6028_R1_Screw_Mount_Top
M3x6 BHCS x 2
M3 Hex-Nut x 4
M3x8 BHCS x 2
DuctSupports (1)
M3x35 BHCS x 2
M3 Washer x 2
6028_R1_M3x35_Spacers

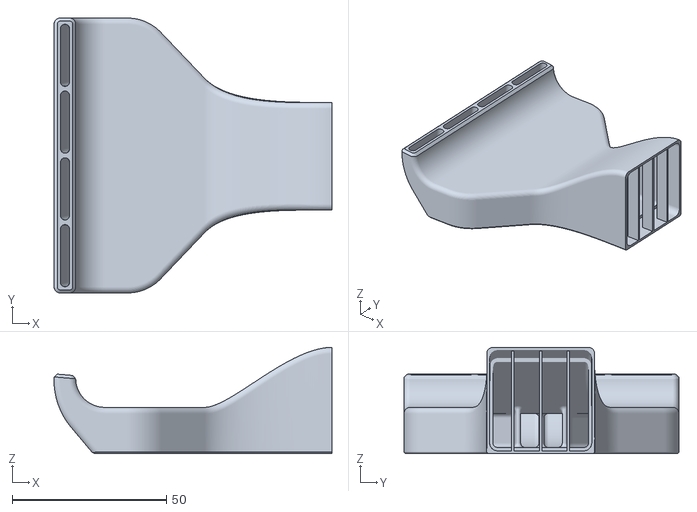
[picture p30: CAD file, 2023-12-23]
ducts/6028/STL/6028_R1_2Piece_Top.stl
90.0 x 89.0 x 34.4

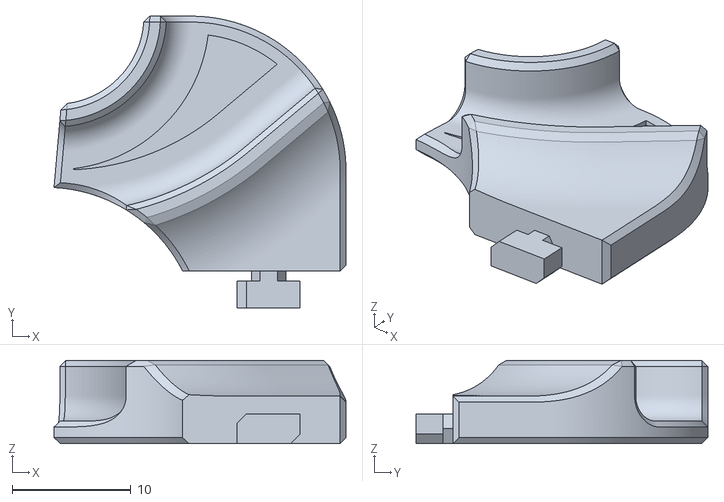
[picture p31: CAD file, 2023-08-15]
ducts/6028/STL/Twist_Mount/6028_R1_Twist_Mount_Top_Right.stl
24.6 x 24.5 x 7.00

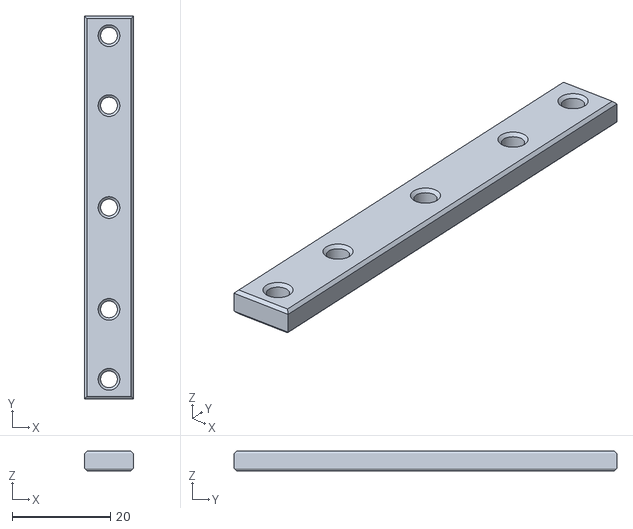
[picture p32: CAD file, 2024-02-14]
ducts/6028/STL/Twist_Mount_Stronger/6028_R1_Twist_Mount_Bottom_Stronger_Bar.stl
10.0 x 77.8 x 4.00

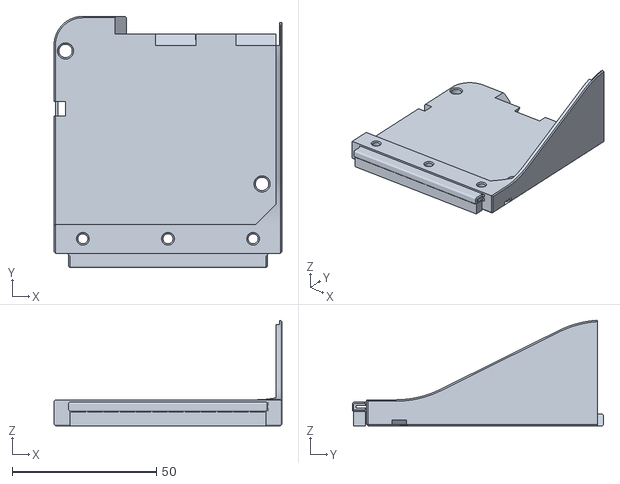
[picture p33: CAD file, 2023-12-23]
ducts/7530/STL/7530_R1_2Piece_Bottom.stl
78.9 x 87.0 x 36.5

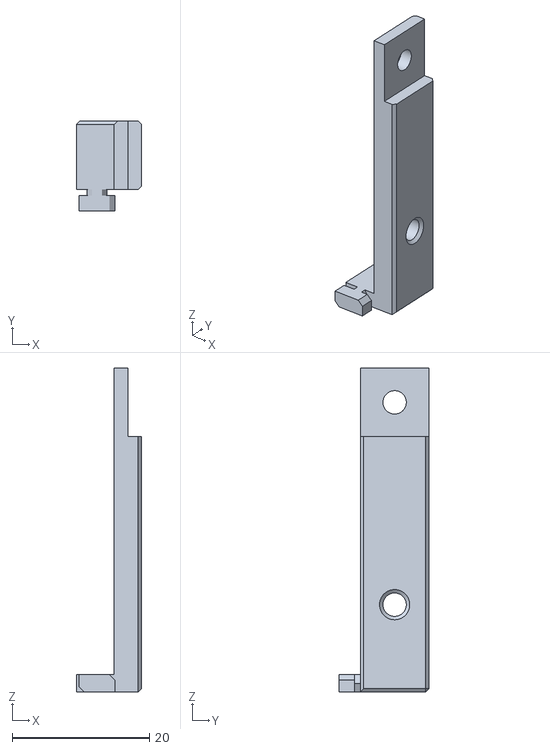
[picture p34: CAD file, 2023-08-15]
ducts/7530/STL/Twist_Mount/7530_R1_Twist_Mount_Bottom_Right.stl
9.50 x 13.1 x 47.2

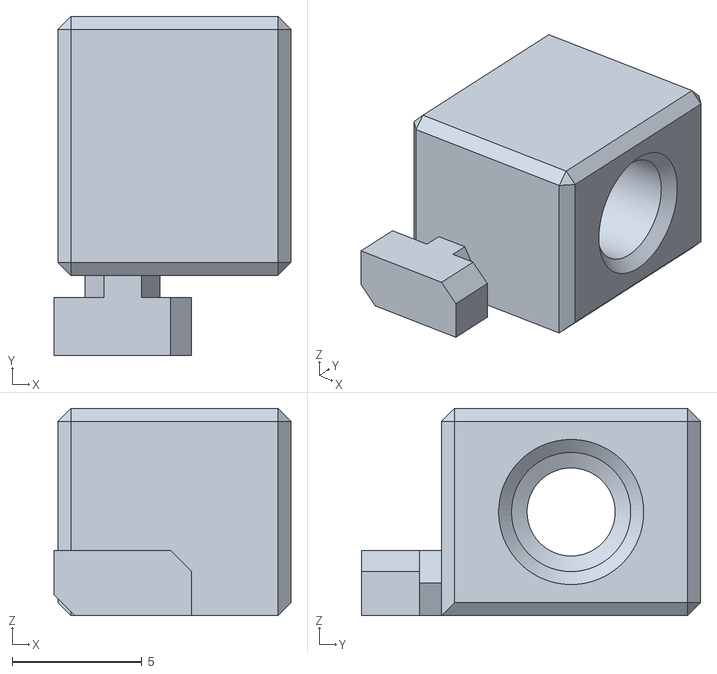
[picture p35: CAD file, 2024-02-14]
ducts/7530/STL/Twist_Mount_Stronger/7530_R1_Twist_Mount_Bottom_Stronger_Right.stl
9.15 x 13.1 x 8.00

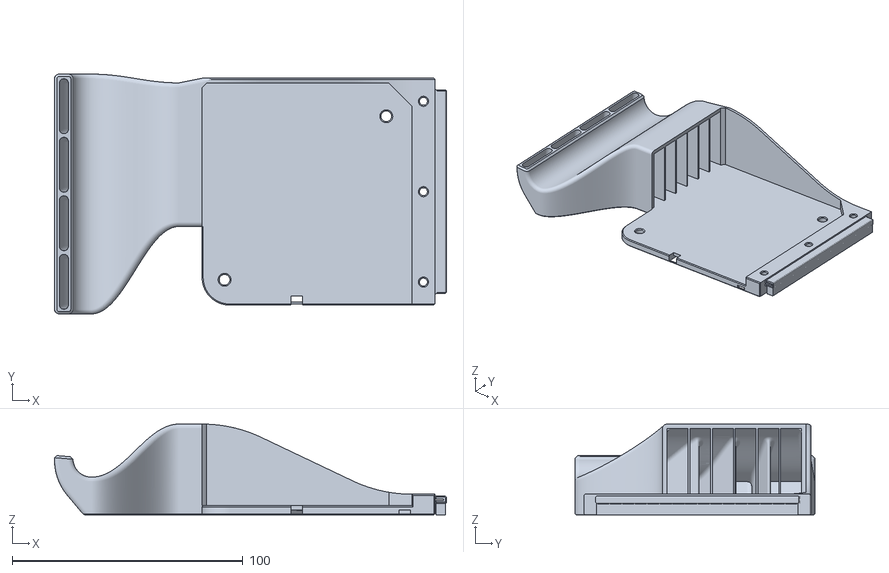
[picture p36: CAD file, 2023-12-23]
ducts/9733/STL/9733_R1_Unibody.stl
170.0 x 104.0 x 39.4

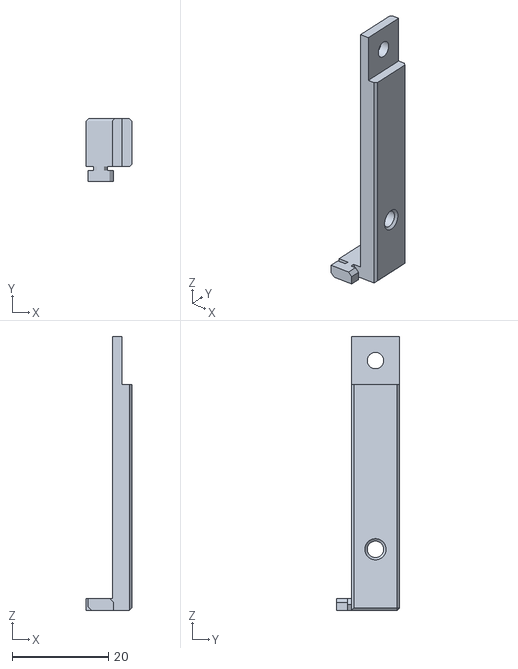
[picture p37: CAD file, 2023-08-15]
ducts/9733/STL/Twist_Mount/9733_R1_Twist_Mount_Bottom_Right.stl
9.50 x 13.1 x 56.9

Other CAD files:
ducts/9733/STL/Twist_Mount_Stronger/9733_R1_Twist_Mount_Bottom_Stronger_Bar.stl
ducts/_Customs/Hex-Zero/7530/CAD/7530_R1_Hex-Zero v9.step
ducts/_Customs/Hex-Zero/7530/STL/7530_R1_Hex-Zero_Right_Top_Twist_Mounts_Left.stl
ducts/_Klicky Compatible/CAD/Klicky Aux Fan v24.step
ducts/12032/STL/12032_R1_Bottom.stl
ducts/12032/STL/12032_R1_Clamp_Block.stl
ducts/12032/STL/12032_Shroud_Top.stl
ducts/12032/STL/Screw_Mount/12032_R1_Bottom_Screw_Mount.stl
ducts/12032/STL/Screw_Mount/12032_R1_Bottom_Screw_Mount_Split_Left.stl
ducts/12032/STL/Screw_Mount/12032_R1_Bottom_Screw_Mount_Split_Right.stl
ducts/12032/STL/Screw_Mount/12032_R1_Screw_Mount_Top_Left.stl
ducts/12032/STL/Screw_Mount/12032_R1_Screw_Mount_Top_Right.stl
ducts/12032/STL/Twist_Mount/12032_R1_Twist_Mount_Bottom_Left.stl
ducts/12032/STL/Twist_Mount/12032_R1_Twist_Mount_Bottom_Right.stl
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

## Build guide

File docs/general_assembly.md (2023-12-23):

# General Assembly Instructions

These Instructions will guide you through the installation process. The assembly process is pretty much the same for all versions, however see the README of your specific duct for additional Information like screw length.

- [50x15mm README](/ducts/5015/README.md)
- [60x28mm README](/ducts/6028/README.md)
- [75x30mm README](/ducts/7530/README.md)
- [97x33mm README](/ducts/9733/README.md)
- [120x32mm README](/ducts/12032/README.md)

## Assembly Instructions

### 1. Remove the built-in Supports

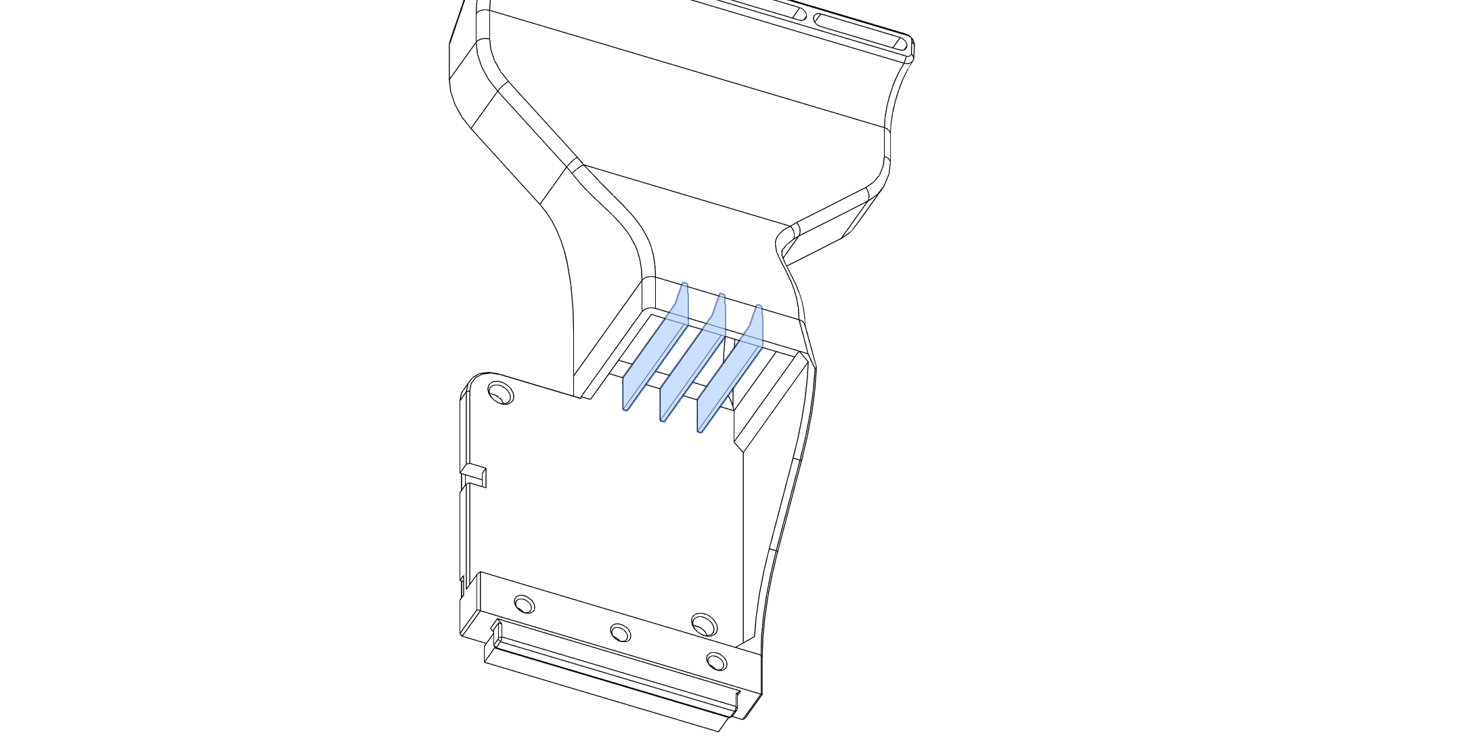
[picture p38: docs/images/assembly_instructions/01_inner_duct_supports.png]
InnerDuctSupports

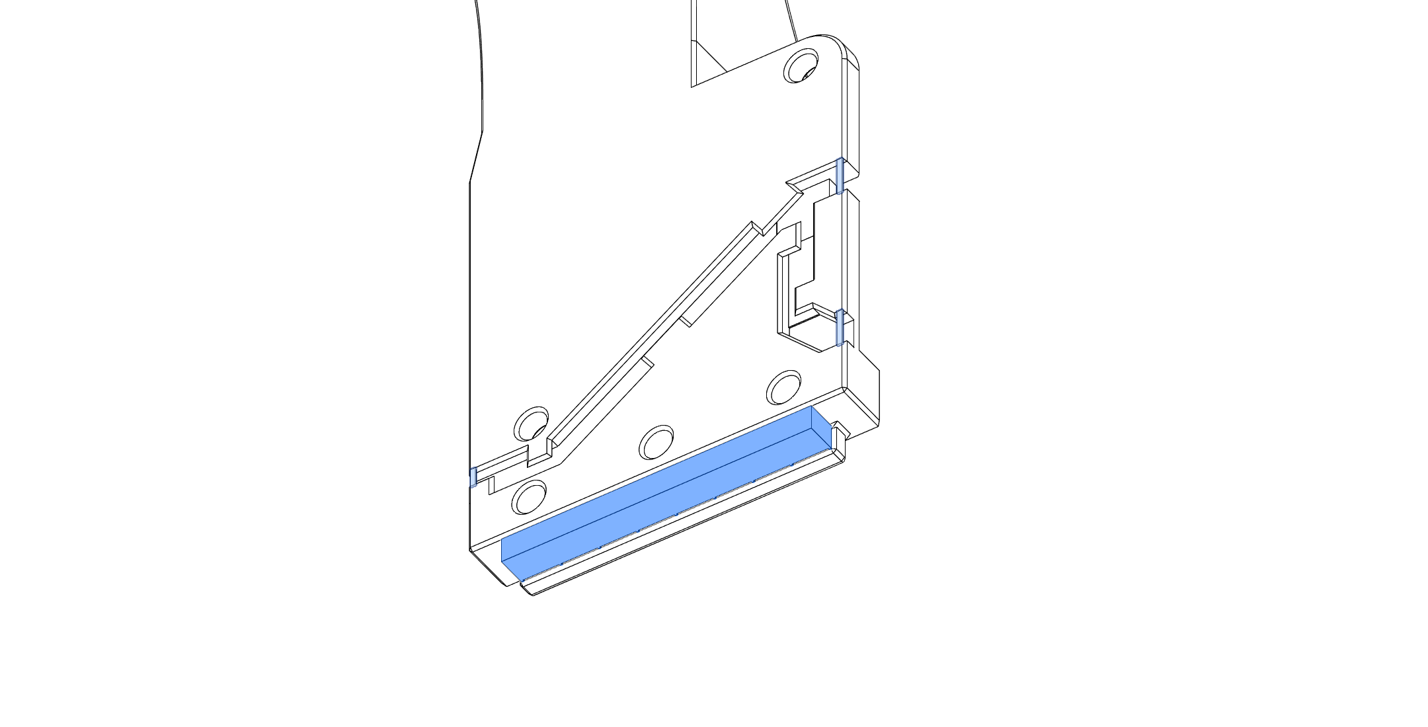
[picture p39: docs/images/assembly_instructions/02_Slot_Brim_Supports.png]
Slot and Brim Supports


#### On the 5015 and 6028 2 Piece Variant you will need to remove some extra supports

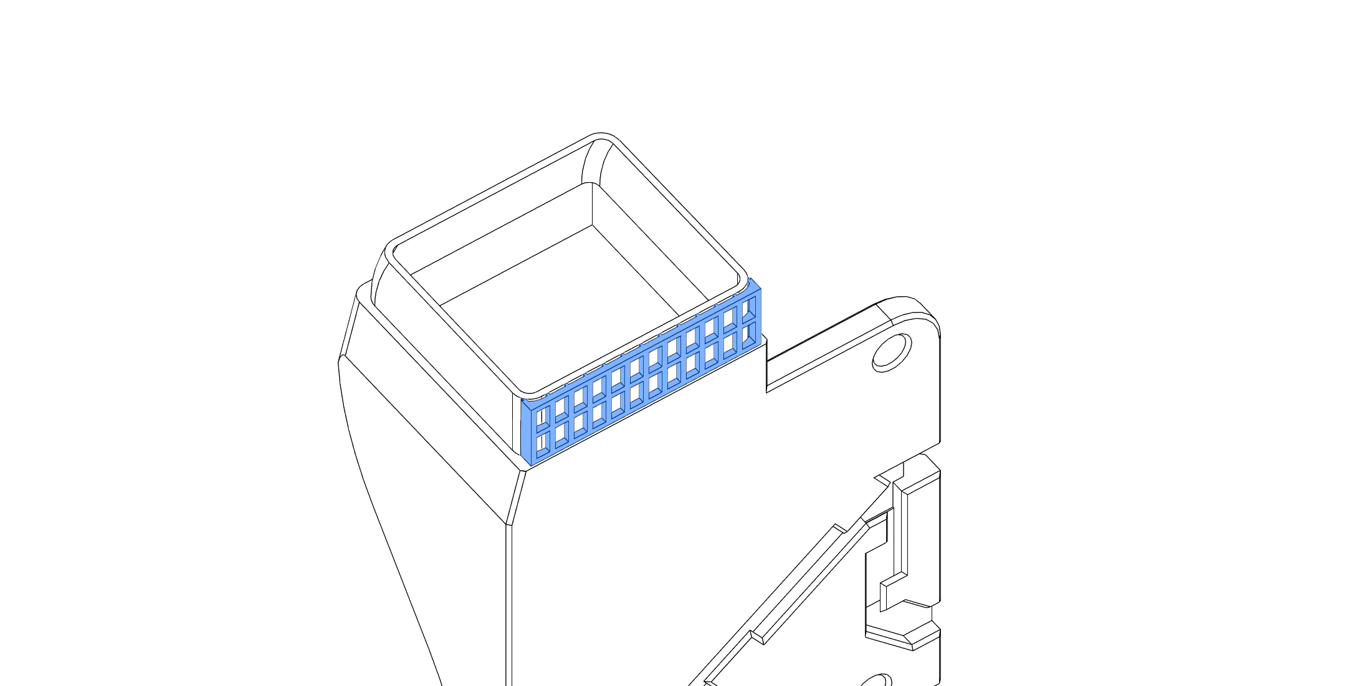
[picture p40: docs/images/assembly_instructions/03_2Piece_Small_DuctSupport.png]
Small 2 Piece Bottom Supports

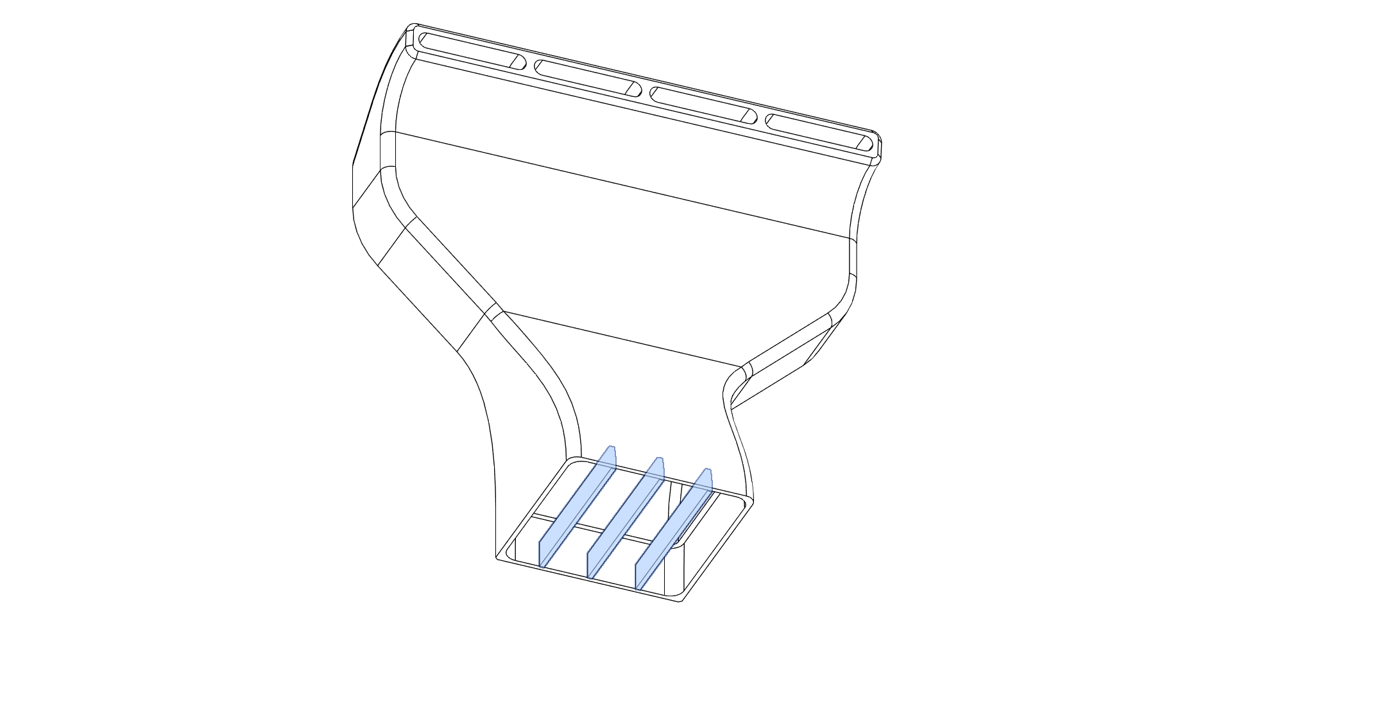
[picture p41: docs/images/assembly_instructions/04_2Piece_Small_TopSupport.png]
Small 2 Piece Top Supports


### 2. If you're using a 2 Piece Variant glue them together at the contact Faces

#### 5015 & 6028

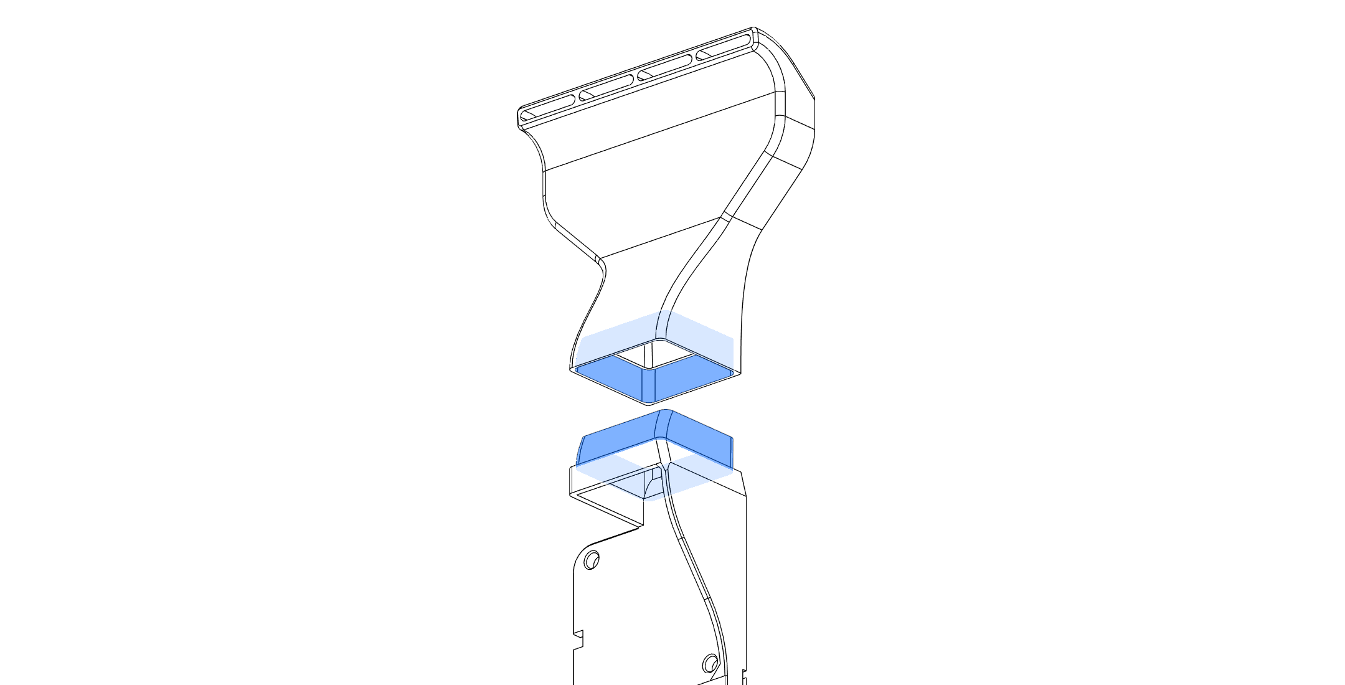
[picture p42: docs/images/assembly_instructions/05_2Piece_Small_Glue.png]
Small 2 Piece Glue


#### 7530 & 9733

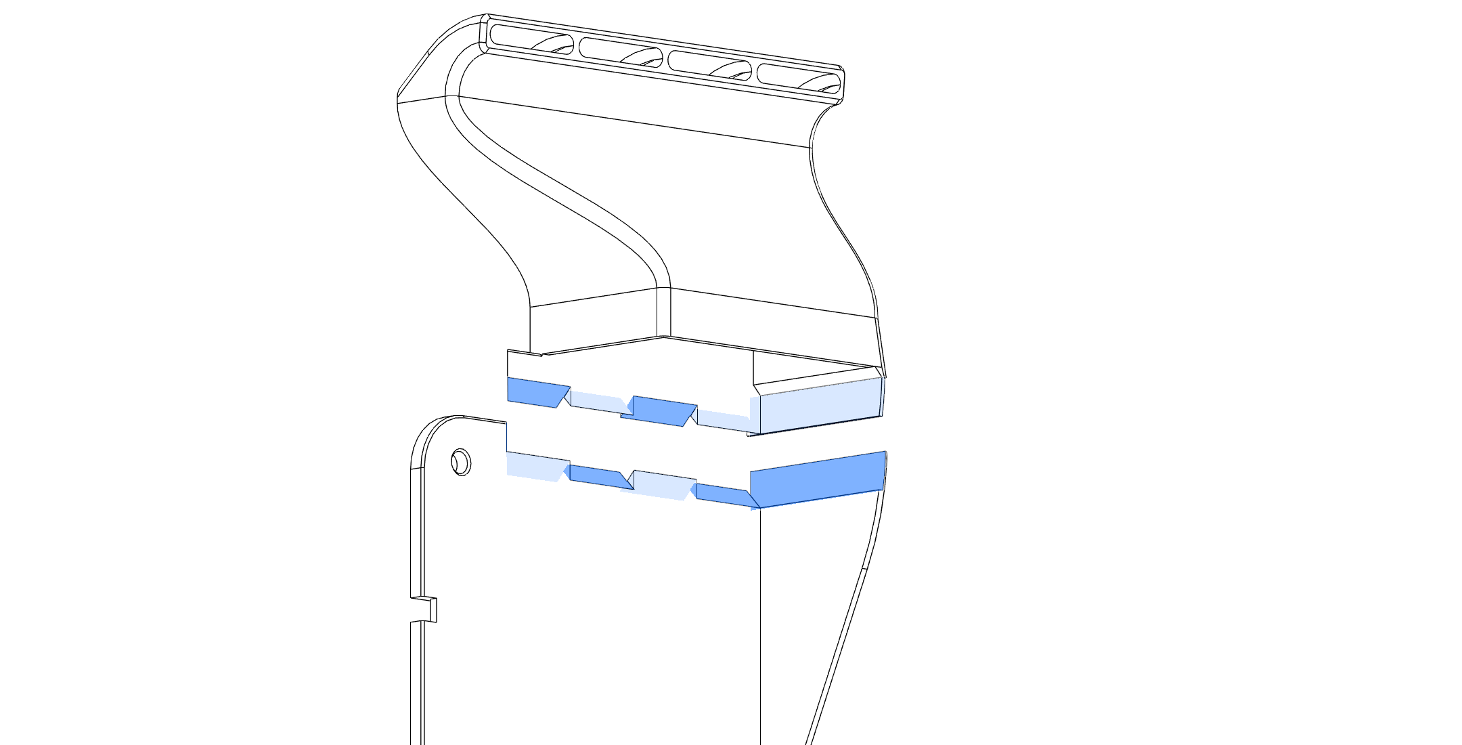
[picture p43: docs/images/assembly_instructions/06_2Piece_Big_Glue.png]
Big 2 Piece Glue


### 3. Insert the Heatsets for the fan from the front

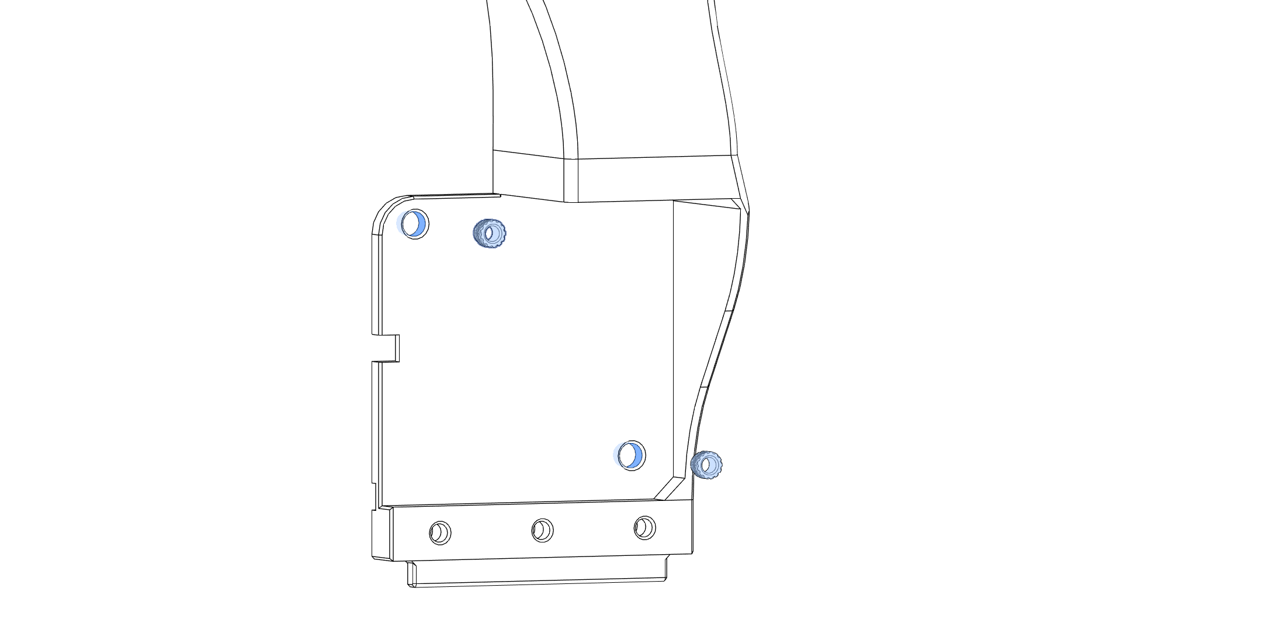
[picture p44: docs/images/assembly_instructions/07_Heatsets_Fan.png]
Heatsets Fan


### 4. Insert the Heatsets for the Mount from the back

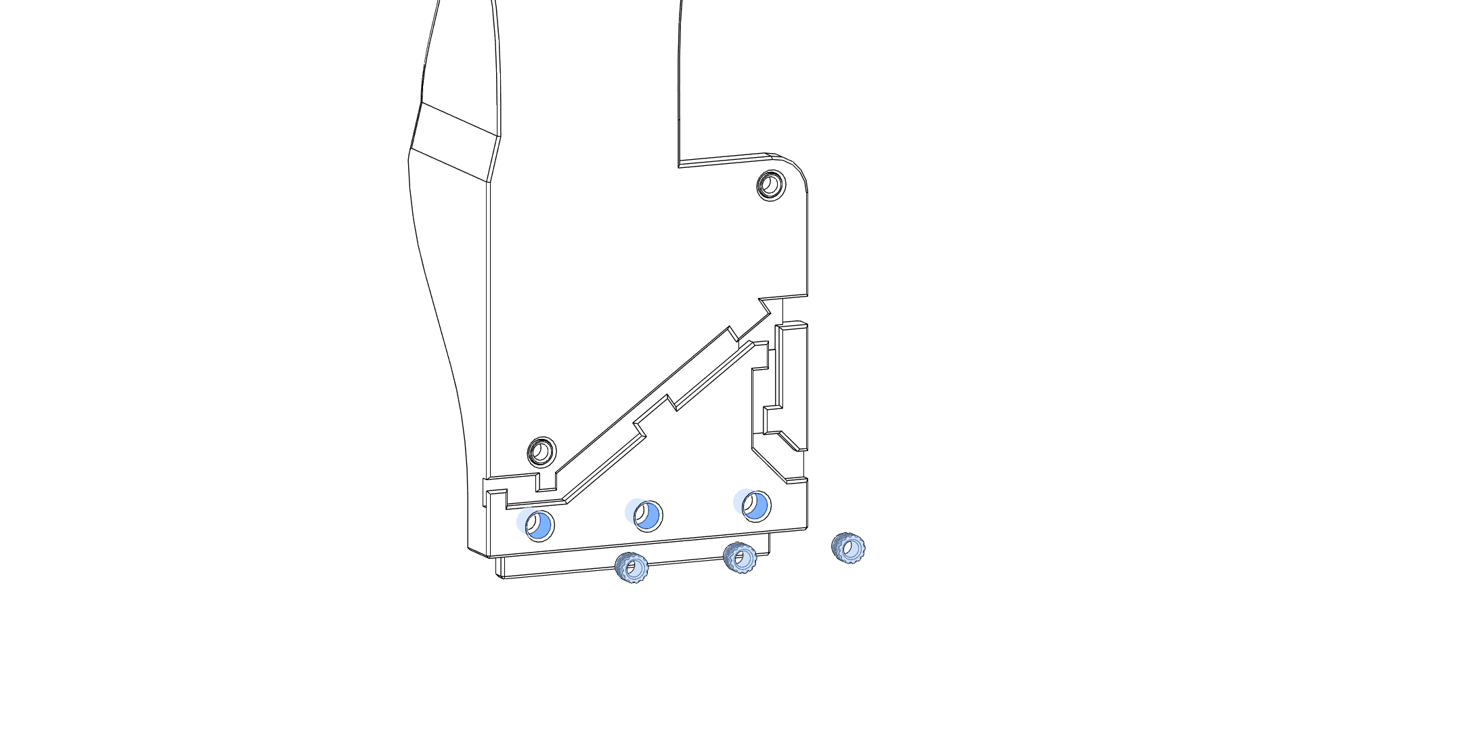
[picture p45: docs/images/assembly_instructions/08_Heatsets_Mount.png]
Heatsets Mount


### 5. Insert the Fan into the duct and secure with the fan screws, washer and spacer if needed. Route the wires through the Channel on the back.

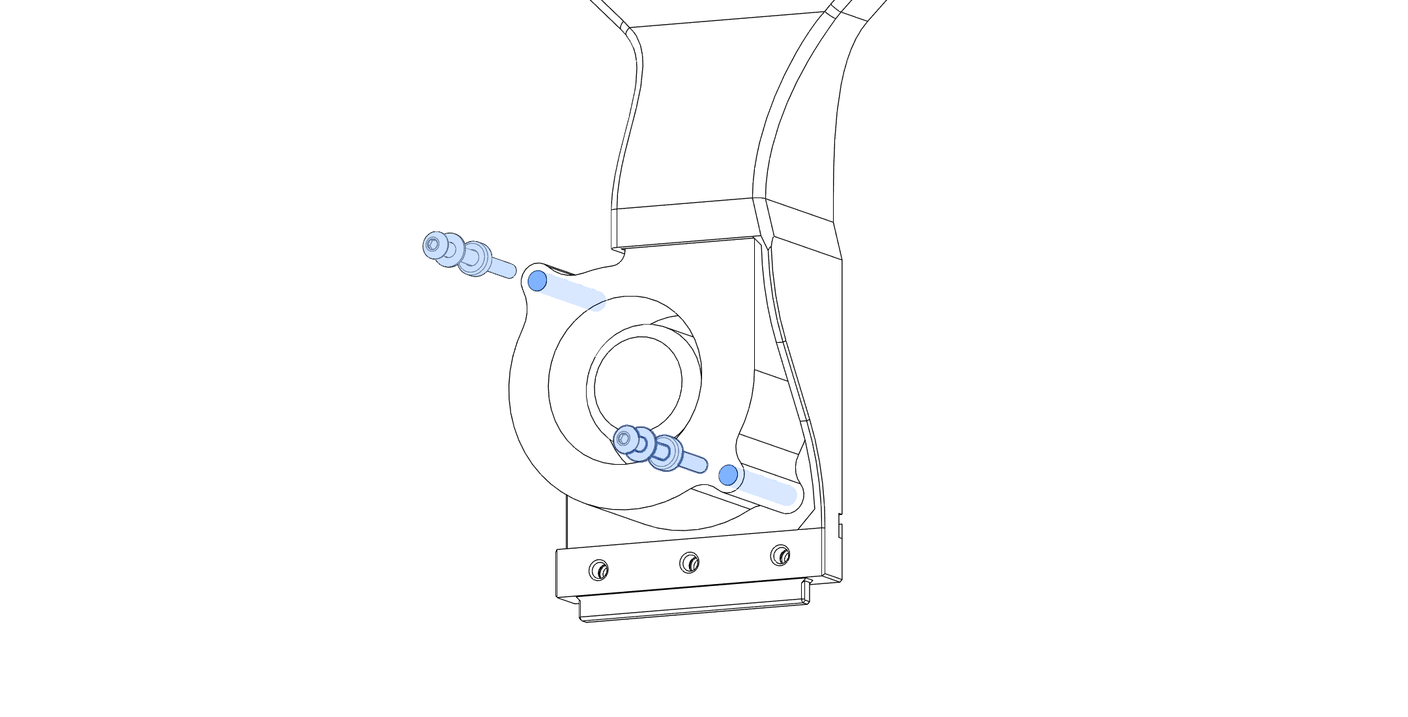
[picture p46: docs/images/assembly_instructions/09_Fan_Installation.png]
Fan Installation


### 6. Apply some VHB-Tape to the inside of the top mounts of your choice. This is mainly to stop the duct from vibrating and rattling around inside the top mounts.

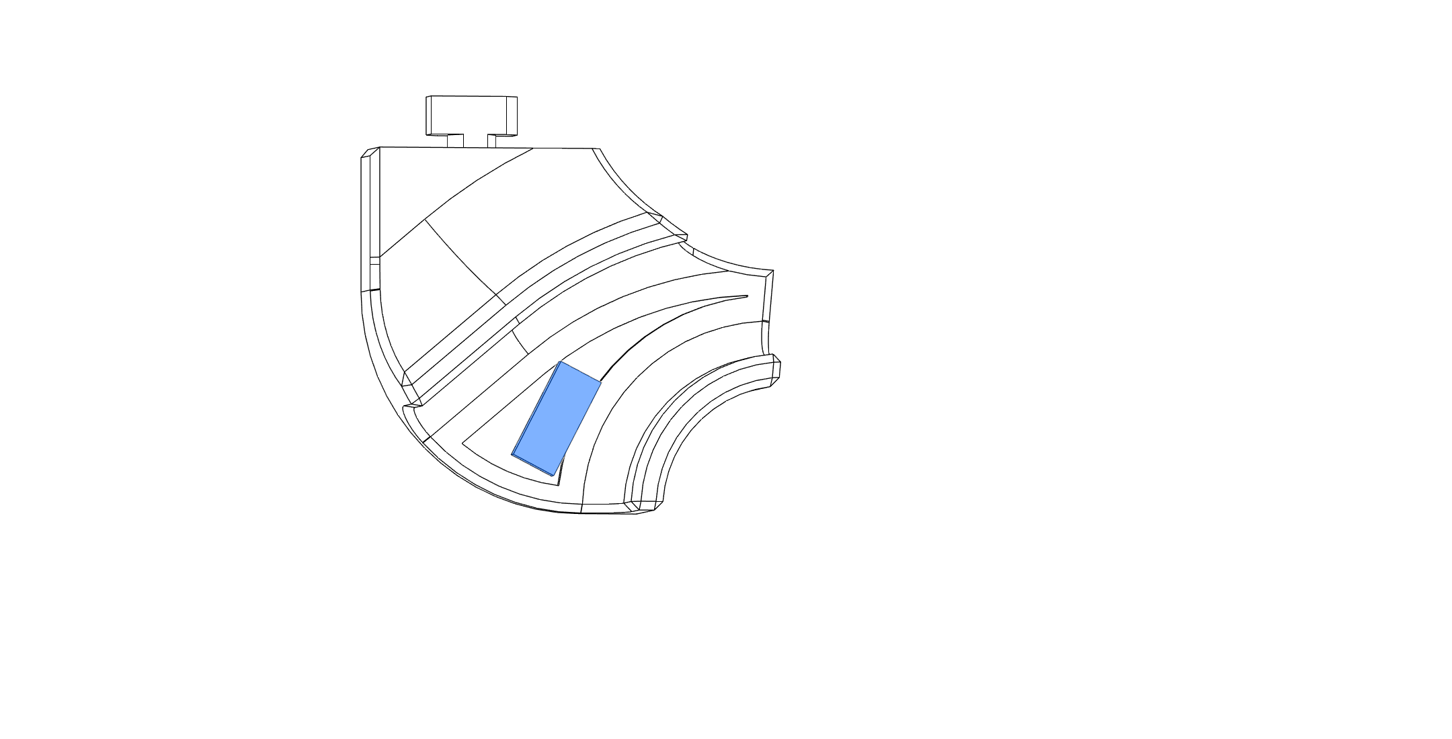
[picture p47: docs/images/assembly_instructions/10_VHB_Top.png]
VHB Top Mount


### 7. Remove the side panel from your V0 for easier access and installation of the duct. This is not strictly needed, but will make installation a lot easier.

### 8. If you want to use the Top Twist mounts it is recommended to insert them now and push them to the side, so they're out of the way for the next step. Insert the Mount and turn them 90° to lock them in place. Do this for both top mounts.

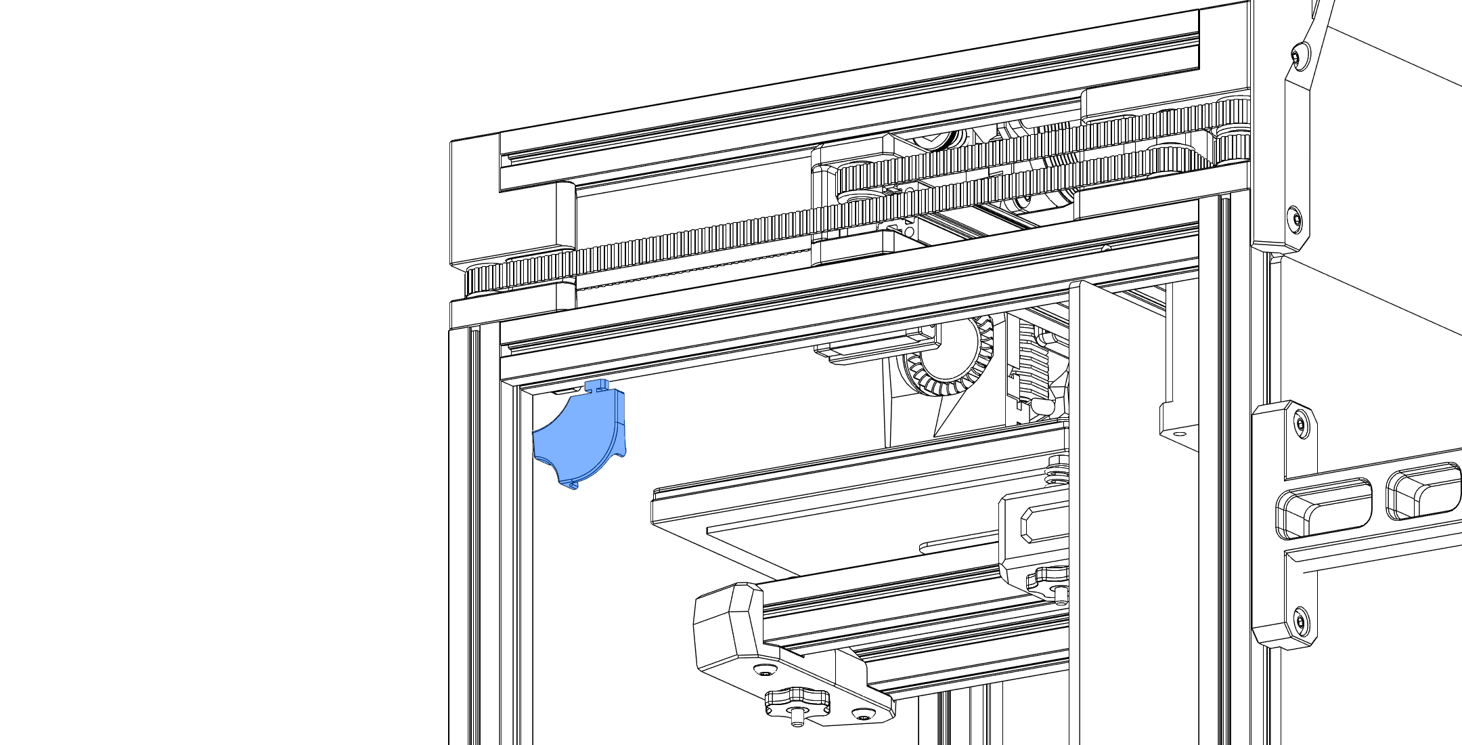
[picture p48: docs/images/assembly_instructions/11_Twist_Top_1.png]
Top Twist Mount Insert

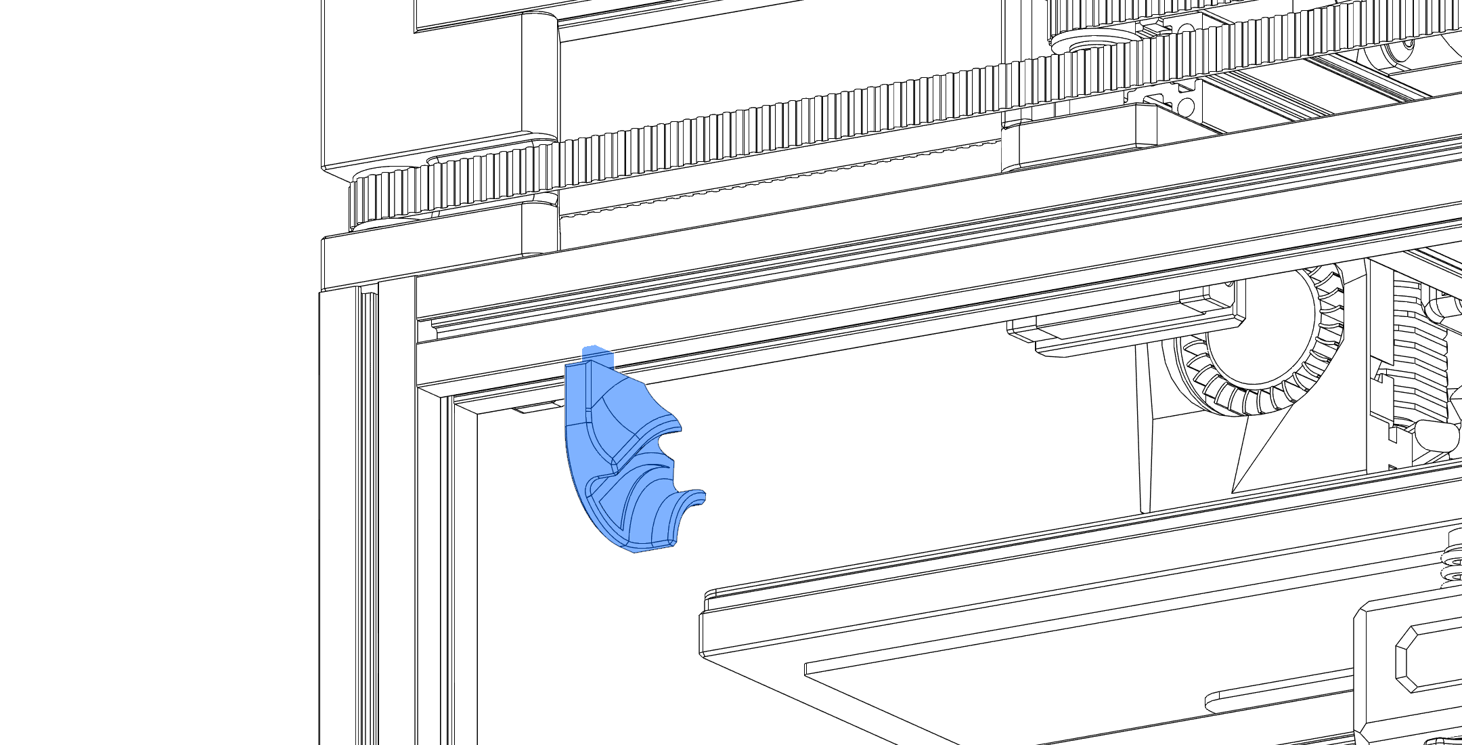
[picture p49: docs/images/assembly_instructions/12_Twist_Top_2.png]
Top Twist Mount Turn


### 9. Insert the duct into the bottom extrusion and align it with the center of the bed

**Tolerances:** If the fit is too tight, and you can't get the duct in the extrusion, sand the bottom part that slots into the extrusion down a bit and try again.
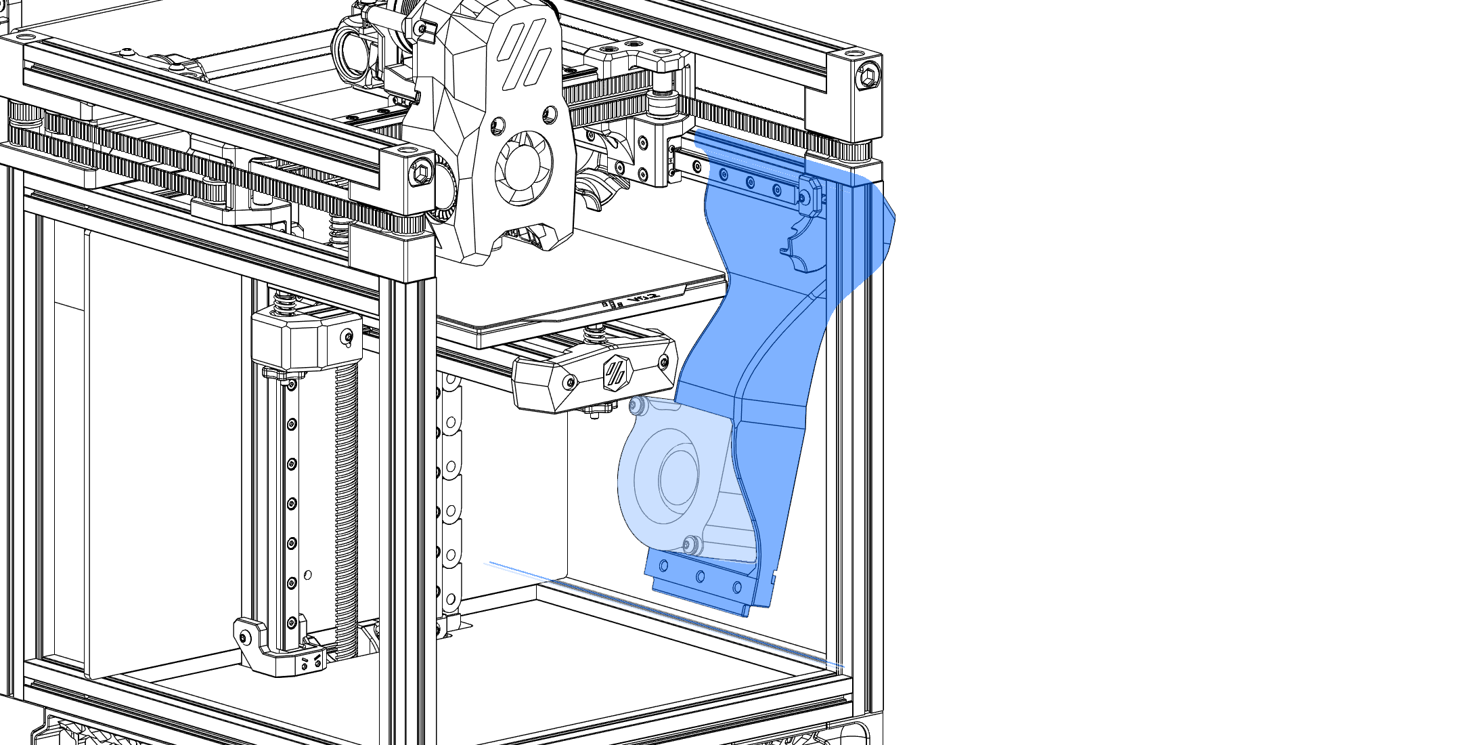
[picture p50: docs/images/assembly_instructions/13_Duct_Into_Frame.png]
Duct into Frame Installation


### 10. Secure the duct to the bottom extrusion with the mount of your choice

#### Twist Mount: Insert into the extrusion, turn 90° and push them against the duct. Secure with 3x M3x12 BHCS

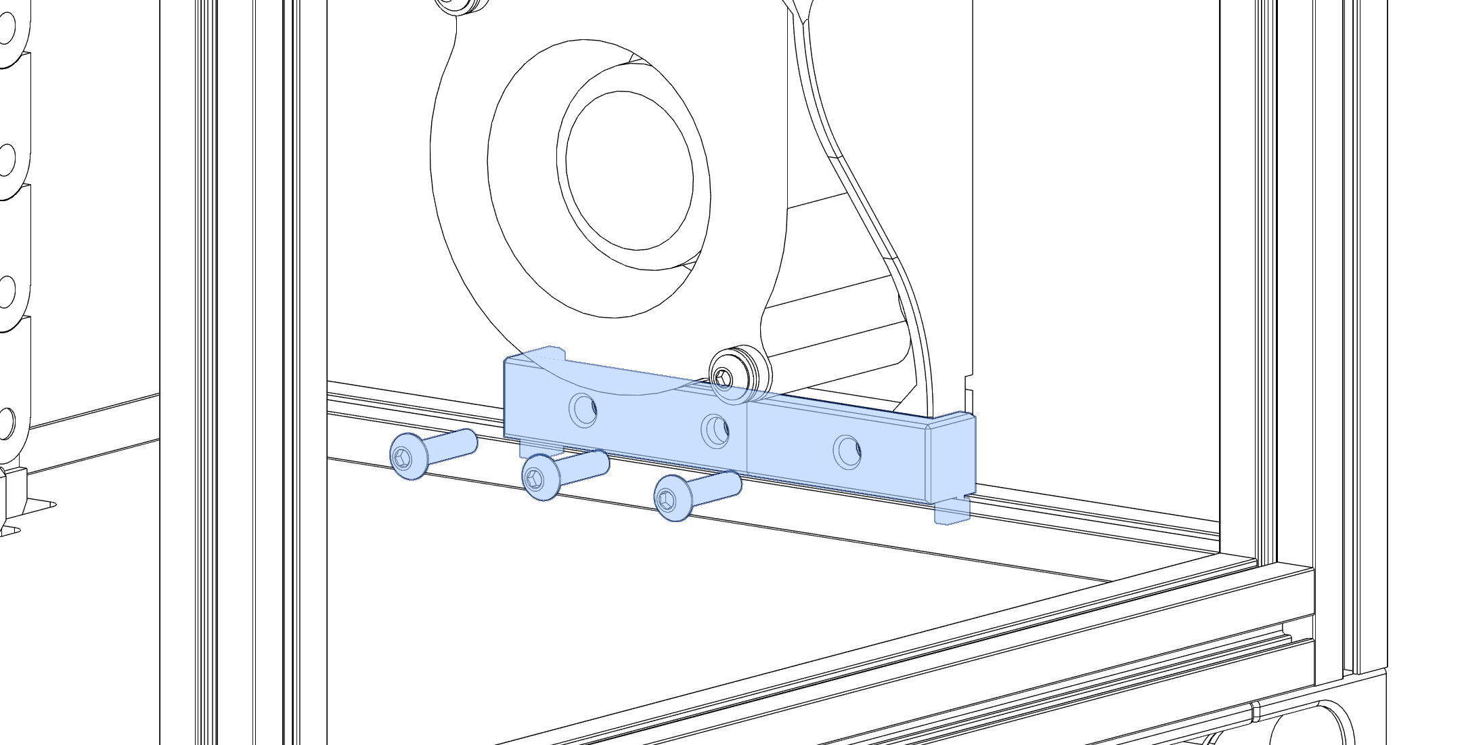
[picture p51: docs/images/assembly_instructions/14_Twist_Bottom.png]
Twist Mount Bottom


#### Screw Mount: Attach the mount with 3x M3x12 BHCS to the duct and with 2x M3x8 BHCS to the Extrusion

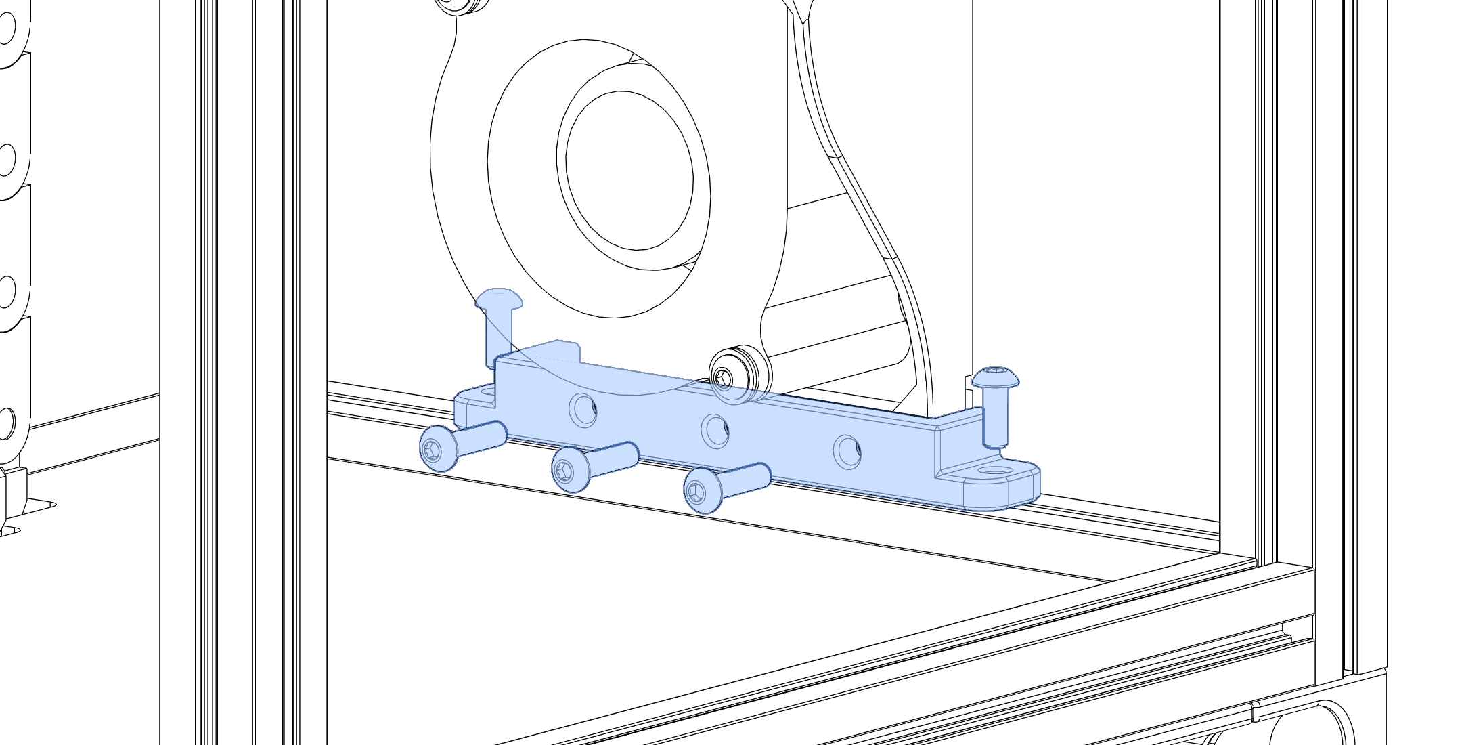
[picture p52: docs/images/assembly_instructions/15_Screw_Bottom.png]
Screw Mount Bottom


#### Clamp Mount: Attach the clamp block to the duct with 3x M3x16 BHCS

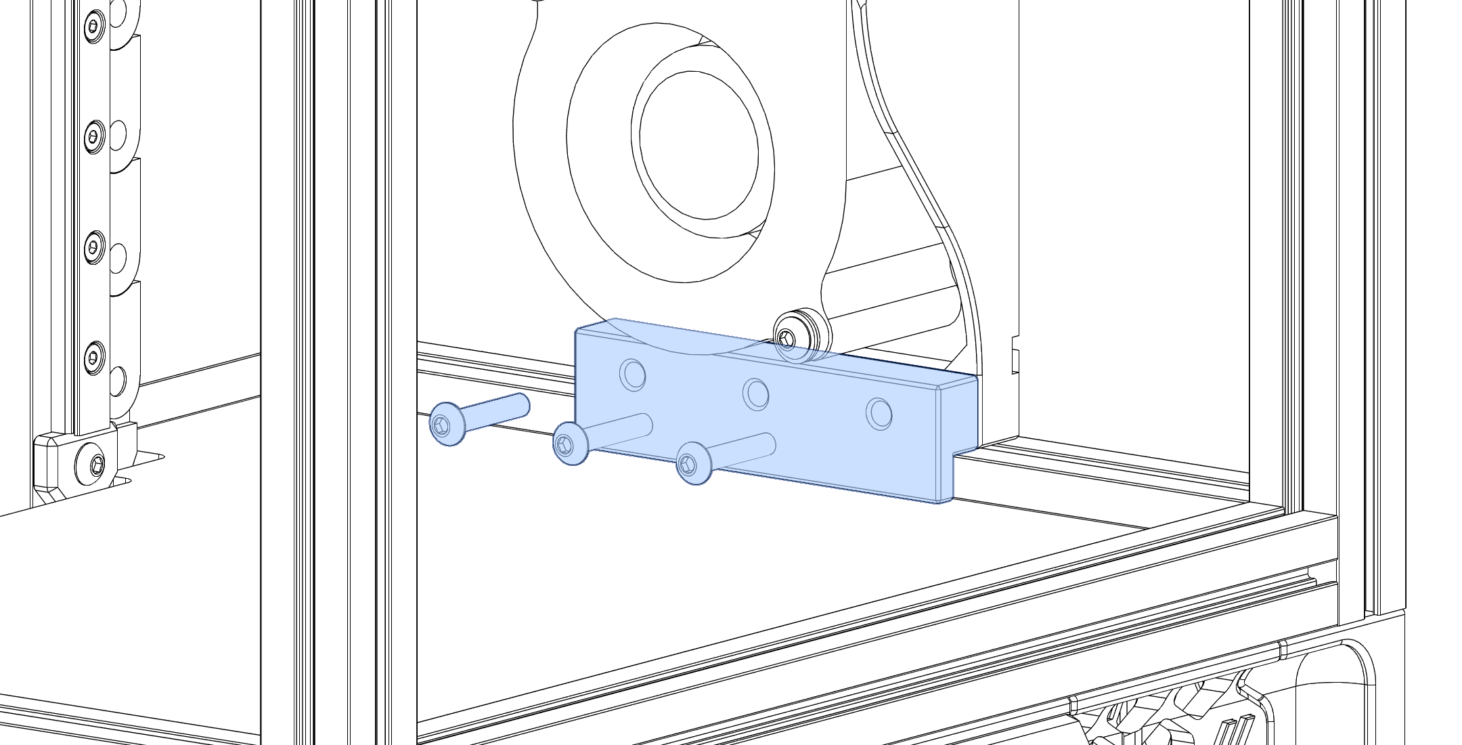
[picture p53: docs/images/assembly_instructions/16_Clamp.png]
Clamp


### 11. Secure the top of the duct.

#### Twist Mount: Slide/Wiggle the Top Mounts to the duct and press them against the duct so the VHB sticks the parts together

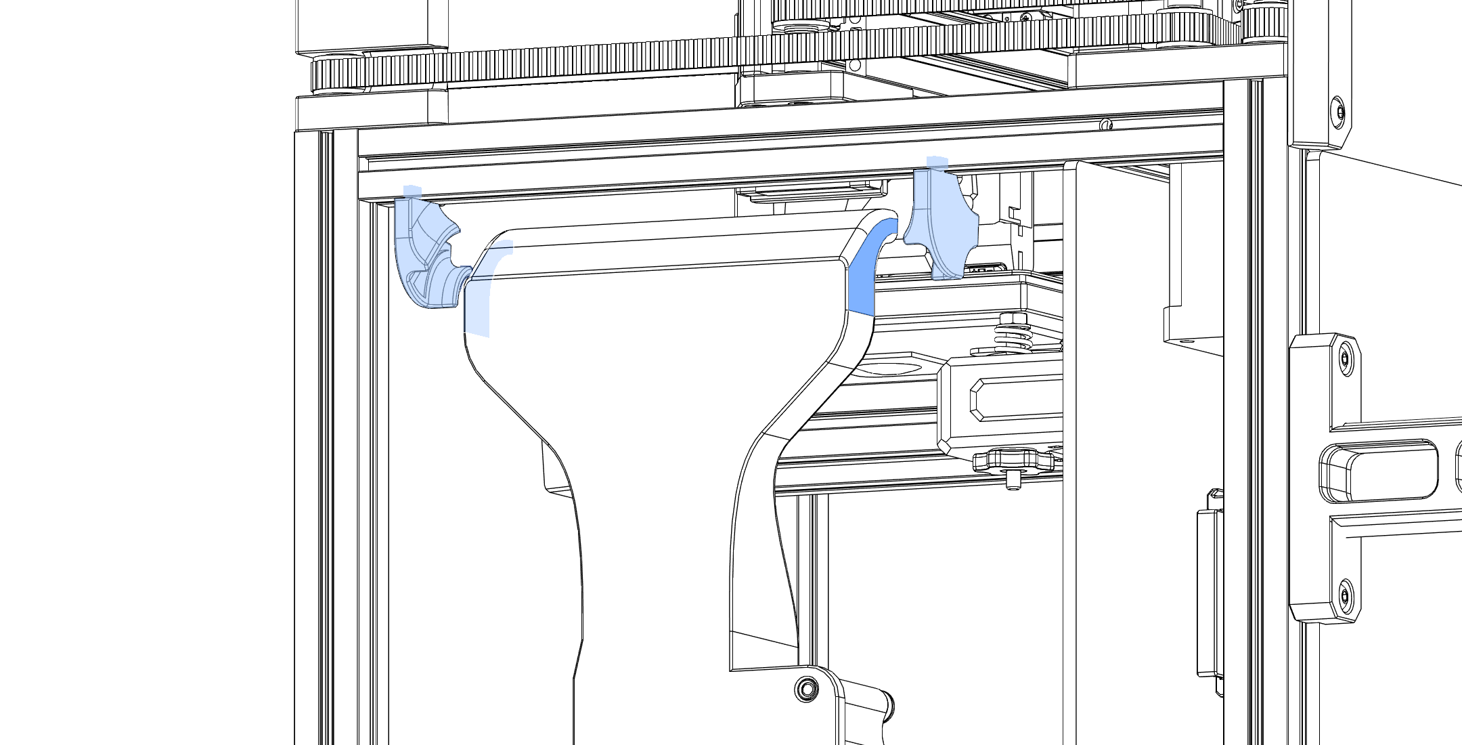
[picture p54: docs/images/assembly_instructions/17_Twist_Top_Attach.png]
Twist Mount Top Attach


#### Screw Mount: Attach the Mounts to the duct with the VHB Tape and secure them to the extrusion with 2 M3x6 BHCS

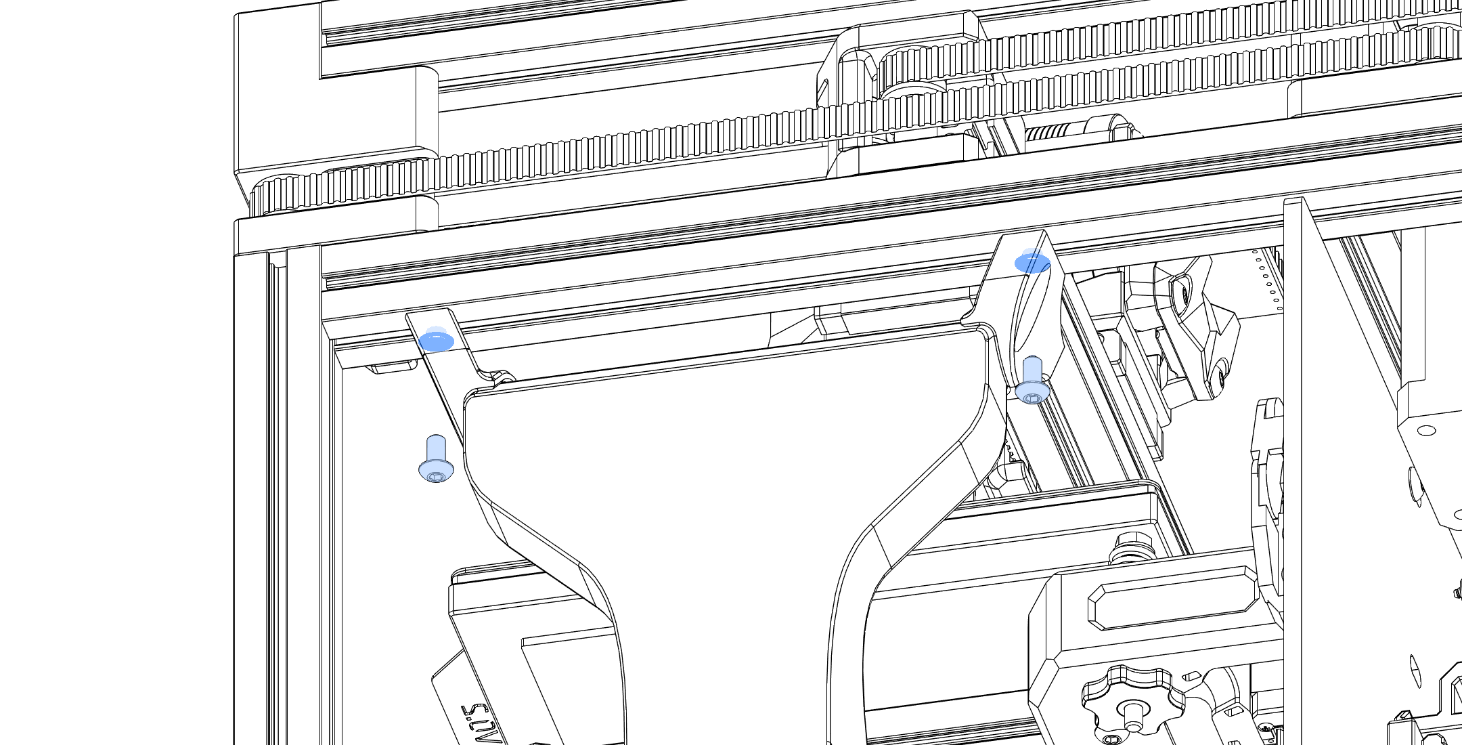
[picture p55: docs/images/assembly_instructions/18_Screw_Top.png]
Screw Mount Top


### 12. Route the wires through the top slot of the bottom extrusion to the electronics compartment.

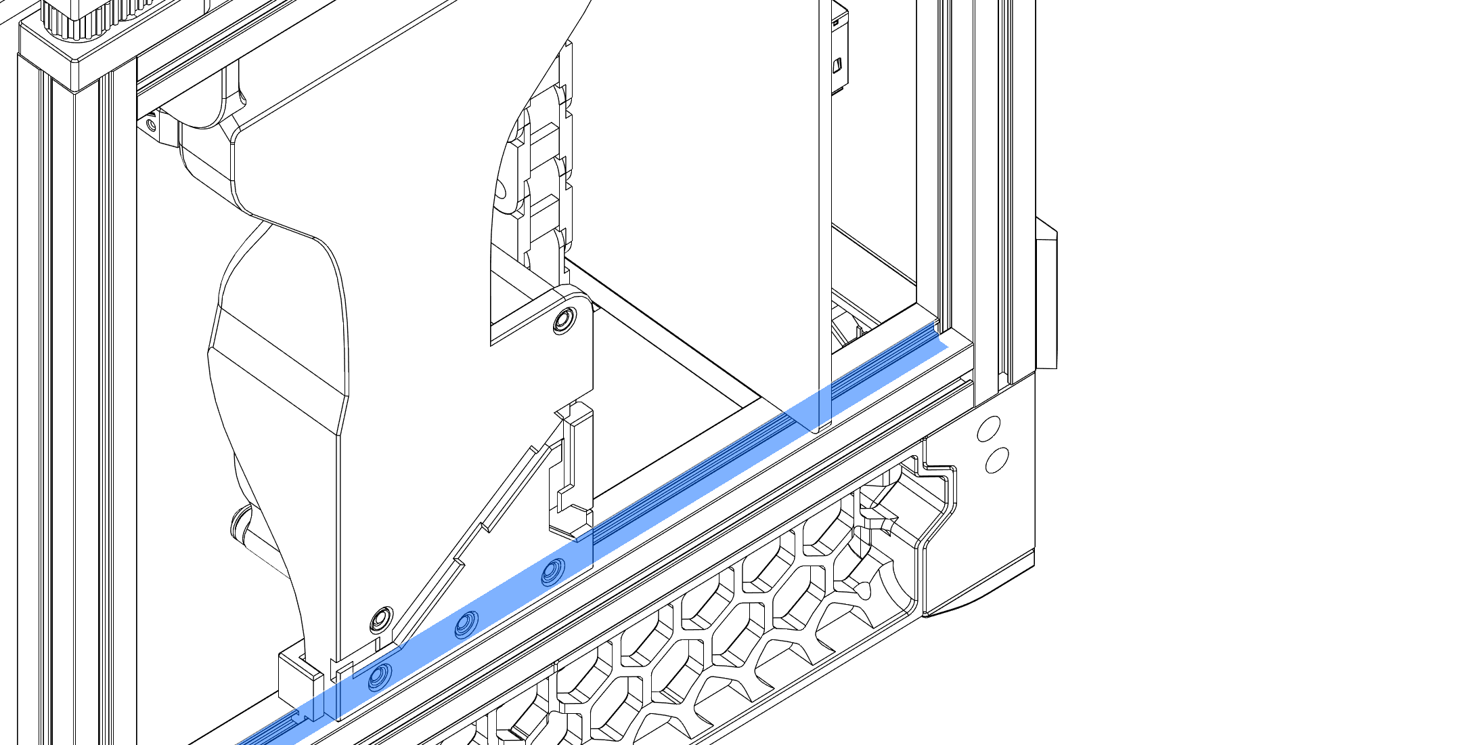
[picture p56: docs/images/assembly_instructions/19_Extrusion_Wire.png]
Wire Routing


### 13. [Connect the Fan](/docs/connecting_fan.md) and [configure the firmware and slicer](/docs/firmware_slicer.md).

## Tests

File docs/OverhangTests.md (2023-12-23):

# Overhang Test (05-2023)
**This Test is currently outdated, as I have not retested with the new R1 Ducts**
- Test File: [Overhang Test by tomi3d](https://www.printables.com/model/126029-overhang-test)
- Filament: PLA - [Redline Filament Yellow](https://www.redline-filament.com/collections/pla-filament/products/premium-pla-gelb)
- Printer: V0.2 with original (Pre r1) Mini-Stealthburner. Enclosure on, Door open, Tophat closed
- Auxiliary Fan was installed on the right side of the printer
- Sliced with OrcaSlicer, same G-Code for all prints only the fan was swapped out or unplugged. Partcooling and Auxiliary Fan were set to 100% after the 3rd layer. Settings are at the [end of this document](#print-settings)

## Results
TL;DR: Bigger Fan means better cooling. The 75x30mm Blower fan seems to be a reasonable choice.

Most of the prints got knocked off the build plate or partially broken because of the severe curling at steeper overhangs. The only one that managed to print fully was the one with the 120x32mm fan. However, as the sample size for each fan was only one print this might have been luck.

With increasing fan size and so with higher air flow the overhangs get cleaner. However, towards the higher end the difference gets quite small, the 120 mm and 97 mm fan almost perform the same in this test.

Also, notable is the fact that the Mini-Stealthburner severely struggles with cooling faces/overhangs that face towards the rear of the printer. This Area is improved quite significantly with the airflow of the larger fans.

Overall I would say the 75x30mm fan provides a good enough performance for the build volume of a V0. Everything bigger seems overkill for "reasonable" print speeds, however if you want to push your printer to the absolute maximum (shoutout [247printing](https://www.youtube.com/watch?v=IRUQBTPgon4)) you probably want to go all the way to the 120 mm one.

The 50x15mm fan doesn't perform very well, however it still improves the overhang-performance by around 10° and chances are generally quite high that 3d-printer builders have some of these lying around already, so you might just try it. Also, there have been some people putting one fan on each side of the printer and being quite happy with the improved cooling, however I have not tested this configuration yet. 
### No Fan
Popped of the bed in the middle of 60°.
Aux Fan Off

### 5015 Fan
Tested Fan: [GDSTIME 5015 24V Dual Ball Bearing Blower Fan](https://www.aliexpress.com/item/32865977791.html)

Arc facing to the left snapped off at the beginning of 70°, the rest printed successfully. The broken arc was glued back on for easier comparison pictures.
Rear Comparison

### 6028 Fan
Tested Fan: [GDSTIME 6028 24V Dual Ball Bearing Blower Fan](https://www.aliexpress.com/item/1005003792895461.html)

Popped of the bed and snapped of the rear facing arc at the beginning of 70°. The broken arc was glued back on for easier comparison pictures.
Rear Comparison

### 7530 Fan
Tested Fan: [GDSTIME 7530 24V Dual Ball Bearing Blower Fan](https://www.aliexpress.com/item/1005002663971820.html)

Popped of the bed and snapped of the left facing arc at the beginning of 60°. The broken arc was glued back on for easier comparison pictures.

While this print failed before most of the others the overhangs look quite a bit better than the ones of the smaller fans.
Rear Comparison

### 9733 Fan
Tested Fan: [GDSTIME 9733 24V Dual Ball Bearing Blower Fan](https://www.aliexpress.com/item/32622626365.html)

Popped of the bed and snapped of the rear facing arc at the beginning of 70°. The broken arc was glued back on for easier comparison pictures.
Rear Comparison

### 12032 Fan
Tested Fan: [GDSTIME 12032 24V Dual Ball Bearing Blower Fan](https://www.aliexpress.com/item/1005005288258849.html)

Managed to print all the way without a catastrophic failure.
Rear Comparison

## Print Settings
The following Settings were used in OrcaSlicer to generate the G-Code
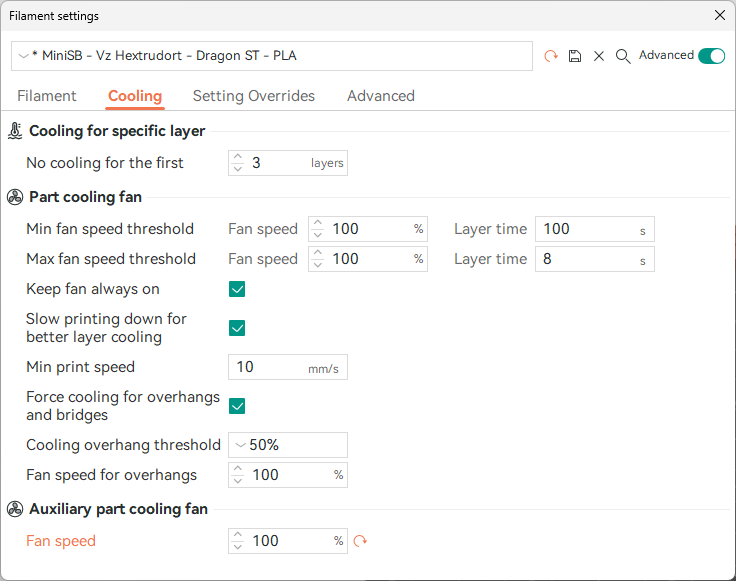
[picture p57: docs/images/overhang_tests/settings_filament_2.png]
Filament Cooling

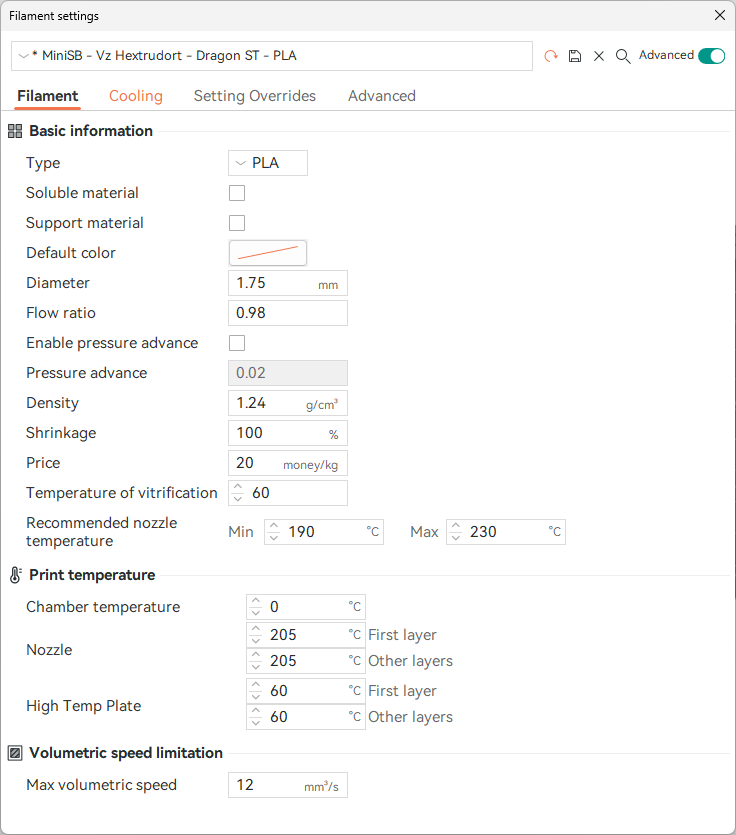
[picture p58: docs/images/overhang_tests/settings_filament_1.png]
Filament Settings

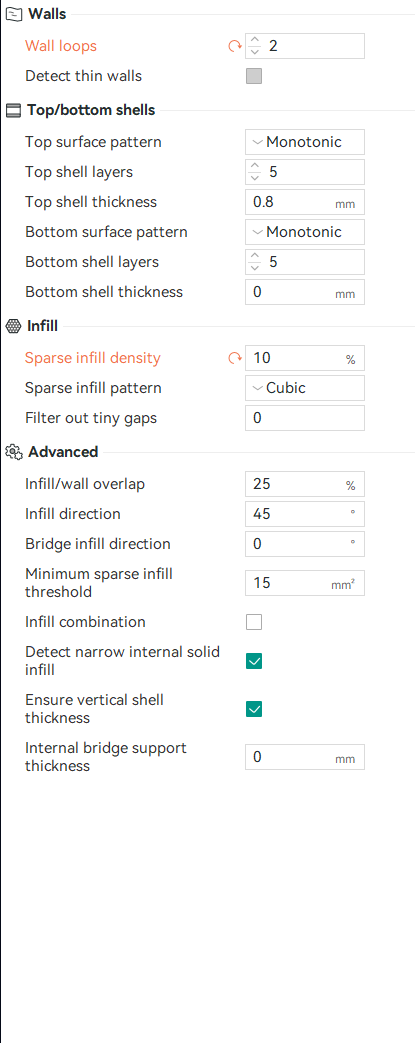
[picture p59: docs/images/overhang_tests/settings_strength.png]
Print Strength

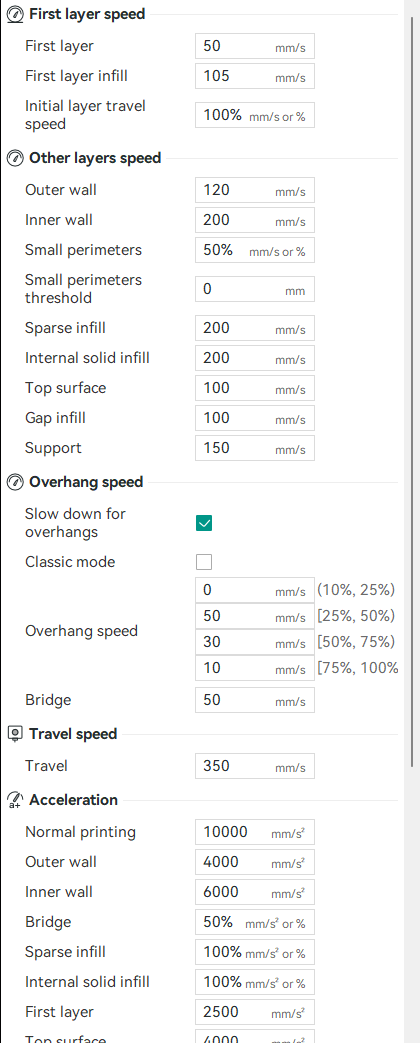
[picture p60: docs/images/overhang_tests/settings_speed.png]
Print Speed


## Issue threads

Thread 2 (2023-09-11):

Makerbeam/kit V0 extrusion compatability

robertsamples, 2023-09-11:
Might be worth considering making the tab that slots into the extrusions more narrow or at least adding a note in documentation. I think the current tab is too thick and is only compatible with wider slot extrusions, a lot of kits use makerbeam-xl style extrusions with a 3.0-3.2 mm slots. Its easy to change in CAD but at least adding a note in documentation about this would be nice.

JackJack3231, 2023-09-11:
The tab is 3.2mm wide (in CAD) to make it a snug fit and the whole thing more solid.
I tried making thinner versions in the past and it made it very loose and more or less pointless (at least on my MakerBeamXL Frame).
The idea is if it is too tight people can sand down the tab a bit to make it slot in easier, however I forgot to add a comment about that in the description/assembly instructions. I added those with f164e16a5d0a651776174ad886a23f61d30a0b10.

I might redesign the tab to give a bit of flex and make it easier to insert for frames with quite narrow slots.

JackJack3231, 2023-12-23:
updated slot design with d0da19ee233d1955b6b2f36744927fc7793aa1e8
Closing this issue for now.

Closed 2023-12-23.

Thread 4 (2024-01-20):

Custom Request

Kosh42, 2024-01-20:
Love the ducts. Any chance of a 12032 Hex Zero compatible if you get time, please?

JackJack3231, 2024-01-20:
Due to the extreme space constraints in the Hex-Zero fitting a 12032 has a bunch of (potential) issues.

Issues when installed on the right side:
The bed frame at the front requires the fan to be shifted back so far, that it would collide with the z-drag chain with the current mounting system for the ducts. So the mounting system would need to be redesigned to clear the drag chain and even then it is quite likely that the drag chain will rub on the fan housing and could potentially get caught (this would need testing in the real world).
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

Issues when installed on the left side:
First of all the mini klicky of the Hexburner can't be used as the dock is in the way.
Second due to the extreme offset of the fan outlet to the print bed center the duct would have a even more aggressive bend in the airpath than the "stock v0" duct.
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

That being said, I think I'll try to make a version that fits on the right side of the printer, as the outlet of the fan is pretty well aligned with the bed. Biggest challenge will be to design mounts that make everything fit, my current idea is to insert heatsets into some of the fan's mounting holes (like in the skirt fans of a V2.4 or Trident).
I should have more free time next month so maybe I can throw something together, but no promises.

JackJack3231, 2024-02-14:
Added a variant to be mounted on the right side with f02e5725cffeb67c84f2ddce15a8a37172ef3aae

Files and more info can be found in the [Folder](https://github.com/JackJack3231/V0-Auxiliary-Fan/tree/main/ducts/_Customs/Hex-Zero/12032).

As this is currently untested and both the clearance and new mounting system could be problematic, I will leave this issue open until I receive feedback on this.

Sooeeren, 2025-04-26:
Great work! I'd love to see a version for the Manta-Ray bed. 👌

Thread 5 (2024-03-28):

Dual 5015 mounting option?

Ataraxia-Mechanica, 2024-03-28:
Larger fans like 12032 fans kick in too slow, I want to mount 2 5015 fans instead which would kick in during bridging and overhangs, then turn off during normal printing, and only 1 5015 doesn't feel like enough cooling.

blazecoding2009, 2024-04-01:
I'd like something like this too, sadly I don't have the cad skills to do this.

JackJack3231, 2024-04-07:
Added a WIP version with eb9c827303de792ef2cc7f71c30de9d7638b8b4d

I haven't tested any of these yet.

Files are available at [ducts/5015_dual](https://github.com/JackJack3231/V0-Auxiliary-Fan/tree/main/ducts/5015_dual)

Currently there is only a unibody version so you will need a larger printer to print this.

blazecoding2009, 2024-04-07:
Nice! I actually got my friend to make one aswell

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

Ataraxia-Mechanica, 2024-04-08:
Time to put the 1 to 4 splitter from Neptune 4 to good use.

blazecoding2009, 2024-04-08:
Mind sending a link @Ataraxia-Mechanica?

Ataraxia-Mechanica, 2024-04-08:
I meant the board inside the quad aux fan assembly. Not sure where to get it separately.
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

Ataraxia-Mechanica, 2024-06-11:
Anybody else want to test this out? I never went with this option and opted to using axial fans instead for a straighter air path since my printer is not enclosed.
https://www.printables.com/model/861403-eardrum-destroyer-voron-v0-4x-4028-auxiliary-fan

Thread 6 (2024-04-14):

Custom Request - Pandora Gantry & Dragon burner - 9733

hudrucan, 2024-04-14:
Try to print 9733 AUX and the Dragon Burner toolhead hit the fan duct on right size, not sure its happened on MiniStealthburner or not.
Its make sensorless homing not correct and not stable.
Can you make a small update with Pandora Gantry, Thanks!

hudrucan, 2024-04-14:
I guess this problem exists on Hex-Zero too, and you have pushed a design for other fan size. Hope you update for 9733.

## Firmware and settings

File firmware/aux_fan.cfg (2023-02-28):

[fan_generic Aux_Fan] 
pin: PIN
max_power: 1.0
shutdown_speed: 0
#cycle_time:
#hardware_pwm:
kick_start_time: 0.2
off_below: 0.25
#tachometer_pin:
#tachometer_ppr:
#tachometer_poll_interval:
#enable_pin:

# Replacement-Macro to control the Fan with M106 P2 and M107 for BambuStudio
# Macro inspired by klipper-github issue https://github.com/Klipper3d/klipper/issues/2174
[gcode_macro M106]
rename_existing: G106
gcode:
    {% if params.P is defined %}
        {% if params.P|int == 2 %}
            {% if params.S is defined %}
                {% if params.S|int == 255 %}
                    {% set realspeed = 1 %}
                {% else %}
                    {% if params.S|int == 0 %}
                        {% set realspeed = 0 %}
                    {% else %}
                        {% set realspeed = params.S|float/255 %}
                    {% endif %}
                {% endif %}
            {% else %}
                {% set realspeed = 1 %}
            {% endif %}

            SET_FAN_SPEED FAN=Aux_Fan SPEED={realspeed}
        {% endif %}
    {% else %}
        {% if params.S is defined %}
          G106 S{params.S}
        {% else %}
          G106 S255
        {% endif %}
    {% endif %}

[gcode_macro M107]
rename_existing: G107
gcode:
    {% if params.P is defined %}
      {% if params.P|int == 2 %}
        SET_FAN_SPEED FAN=Aux_Fan SPEED=0
      {% endif %}      
    {% else %}
      SET_FAN_SPEED FAN=Aux_Fan SPEED=0  
      G107
    {% endif %}
    
###############################################    
### Display control
### Adds Fan controls for Auxfan to Displays Control section
###############################################

[menu __main __control __auxfanonoff]
type: input
enable: {'fan_generic Aux_Fan' in printer}
name: Aux Fan: {'ON ' if menu.input else 'OFF'}
input: {printer['fan_generic Aux_Fan'].speed}
input_min: 0
input_max: 1
input_step: 1
index: 9 # Place it right beneath partcooling fan controls
gcode:
    M106 P2 S{255 if menu.input else 0}

[menu __main __control __auxfanspeed]
type: input
enable: {'fan_generic Aux_Fan' in printer}
name: Aux speed: {'%3d' % (menu.input*100)}%
input: {printer['fan_generic Aux_Fan'].speed}
input_min: 0
input_max: 1
input_step: 0.01
index: 10 # Place it right beneath partcooling fan controls
gcode:
    SET_FAN_SPEED FAN=Aux_Fan SPEED={menu.input}

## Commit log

2023-02-28 Initial Release
    [Aux Fan 2 Part v4.step, Aux Fan 2 Part v9.step, Aux Fan v21.step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]
2023-02-28 update firmware config
    [aux_fan.cfg]
2023-02-28 Update aux_fan.cfg
    add Fan-Controls to Displays
    [aux_fan.cfg]
2023-05-01 Make shroud actually 4mm thick
    Back of shroud was only 3.8mm thick, so 0.2 mm shorter than the heatsets, fixed now
    [Aux Fan 2 Part v10.step, Aux Fan v31.step, Clamp_Block.stl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]
2023-05-21 Big Fan Update
    - Add Fan Ducts for 6028, 7530, 9733 and 12032 Blower Fans
    - Add Comparision Pictures of the cooling performance
    - Restructure Repository to better accomodate all the different options
    [12032 v24.step, 12032_Clamp.stl, 12032_Shroud_Bottom.stl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]
2023-05-28 Update instructions and images
    [7530_spacer_1.6mm_x2.stl]
2023-05-29 small visual updates
    [12032 v24.step, 12032 v30.step, 12032_Clamp.stl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]
2023-05-29 Export up to date 5015 CAD
    [5015 2 Part v11.step, 5015 Unibody v35.step]
2023-06-24 Changed 12032 duct to be centered
    [12032 v30.step, 12032 v31.step, 12032_Shroud_Top.stl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]
2023-08-15 R1 Update
    [12032 v31.step, 12032_Clamp.stl, 12032_R1_Bottom.stl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]
2023-08-25 Add 5015 & 6028 ducts with clearance for klicky
    [5015_Klicky_Unibody.stl, 6028_Klicky_Unibody.stl, Klicky_Screwmount_Top_Left.stl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]
2023-09-11 Add Notes about Slot Tolerances
2023-12-23 Update slot part, Add Customs
    [12032_R1_Bottom.stl, 5015_Klicky_Unibody.stl, 5015_R1 v76.step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]
2024-02-14 Add 12032 Hex-Zero duct.
    [12032_R1_Hex-Zero_Bottom_Screw-Mount_x2.stl, 12032_R1_Hex-Zero_Bottom_Twist-Mount_x2.stl, 12032_R1_Hex-Zero_Top_Screw-Mount_Left.stl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]
2024-02-14 Add stronger bottom twist mount
    [12032_R1_Bottom_Screw_Mount.stl, 12032_R1_Bottom_Screw_Mount_Split_Left.stl, 12032_R1_Bottom_Screw_Mount_Split_Right.stl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]
2024-04-07 Add WIP dual 5015 duct
    [Dual_5015_R1 v8.step, Dual_5015_ScrewMount_Bottom.stl, Dual_5015_ScrewMount_Top_Left.stl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]
